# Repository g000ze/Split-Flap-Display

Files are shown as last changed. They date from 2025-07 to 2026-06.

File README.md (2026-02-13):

## Intro
Older people (like me) look back with nostalgia at train stations and airports, middle-aged people are captivated by technology, and the younger generation is excited by the clattering sound combined with the non-virtual movement. The split flap display remains a fascinating display panel for text and small animations.

One day, while watching a video about split flap displays, I suddenly felt the desire to own one. After a relatively short research, I realized that only a few manufacturers build such displays. There are, for example, [Oat Foundry](https://www.oatfoundry.com/), [Vestaboard](https://www.vestaboard.com/), [Scott Bezek](https://github.com/scottbez1/splitflap) or the one called "Split Flap Display Manufacturer." No matter which manufacturer you choose, the displays are either very expensive or don't meet my requirements. So I decided to try building one myself.

DIY Split Flap Display on YouTube (https://www.youtube.com/watch?v=Lept-73BvrE)

A typical split flap display looks best when it can display text. This text is naturally composed of characters, i.e., letters, numbers, and special characters. Optionally, symbols, colors, or images can also be displayed. A character is represented on the display by a so-called module. A module consists of a housing, a stepper motor, a motor driver, a PCB that connects the driver and the motor, a carousel, 50 flaps for the characters, and, of course, various spacers and screws that hold the whole thing together. A magnetic sensor (Hall effect sensor) is also integrated into the carousel, which tells the microprocessor when position 0 or the home position has been reached.

As already mentioned, a single module produces little effect, so we want multiple modules for a display to achieve an intense visual effect. I decided to control eight modules with an [Arduino Micro](https://docs.arduino.cc/hardware/micro/). The modules therefore always come in units of eight. The Micro offers 20 digital input/output pins. Two of these are required per module: an output pin as a stepper for the driver and an input pin for the Hall effect sensor to determine the feedback for a full rotation of the carousel. This means a total of 16 Arduino pins are used for eight modules. The Arduino, in turn, is placed on the backplane PCB, where the modules are plugged into so-called card edge connectors. This PCB primarily controls two things:
- The digital communication between the Arduino and the modules (drivers & Hall sensors)
- The power supply for all electronics, including the motors

**Animation of spinning spool using OpenSCAD**

Spinning Carousel (https://github.com/user-attachments/assets/af98eea6-6dcd-4d9f-962c-459cd9d655be)

[![Exploded View]](https://github.com/user-attachments/assets/ecffe0bf-9c8d-47f0-b8ce-c02ede4a916f)

## The Housing
The housing is used to position the motor, along with the carousel and flaps, as well as the PCB with the Hall sensor. If everything is exactly right, the flaps will drop at the right time and the magnet will move correctly over the sensor. I used 0.8 mm sheet steel for the housing. The 3D OpenSCAD drawing can be found [here](https://github.com/g000ze/Split-Flap-Display/blob/main/OpenSCAD/Chassis.scad). I found a company in Switzerland called [Blexon](https://blexon.com), that will punch and bend the housing according to my specifications.

Housing

## The Stepper Motor
Normally, Nema 17 stepper motors are mounted on the side where the shaft is located. This display is different; the motor must be mounted on one side, and the shaft, where the carousel is screwed to, must be on the opposite side. The [17HS13-0404D](https://www.omc-stepperonline.com/de/doppel-schacht-nema-17-bipolar-1-8deg-26ncm-36-8oz-in-0-4a-12v-42x34mm-4-draehte-17hs13-0404d) is the only Nema 17 I could find with the shaft on the opposite side from where it is mounted. This motor is actually a "dual shaft" motor. The 17HS13-0404D is powered by +12 volts.

17HS13-0404D

## The Driver
To operate a stepper motor, you need a driver. There are many. I experimented with stepper motor drivers for a long time until I finally came across the [TMC2208](https://www.digikey.ch/de/products/detail/watterott-electronic-gmbh/20170003-002/10071142) "Silent Step Stick" from [Watterott](https://learn.watterott.com/de/silentstepstick/). This driver allows the 17HS13-0404D to run almost silently. Finally, the sound of a split-flap display plays a crucial role. We want to hear only the flaps clattering, not the motors.

## The PCBs
Two different types of PCBs are required. One is a small PCB that is attached to each module. It essentially carries the driver and the Hall sensor. The other is the backplane PCB, which connects the Arduino's electronic wires to the eight modules via card-edge connectors. The six connections that run via the card-edge connectors are:
- Hall sensor
- GND
- +5V
- Step
- GND
- +12V

The TMC2208 and the Hall sensor on the module PCB each operate at +5 VCC, while the motor naturally requires 12 volts.

Module markiert
Backplane markiert

## The Carousel
The Carousel is attached to the pouley on the motor shaft so that it can be rotated by the steppermotor. It also holds the 50 flaps in position. The stepper motor is located inside the carousel. With its 82mm diameter, the carousel fits perfectly around the motor and there's enough space for the 50 flap positions. The two wheels are different, as the left wheel contains spokes, while the right wheel is open.

Carousel

I decided to use [3mm PVC plates](https://www.vink.ch/wa_files/Produktblatt_20PVC-U_20TROVIDUR_20EC_205_3_2015_20Ind.pdf) for the carousel. A company named [Waterjet](https://www.waterjet.ch/) located in Switzerland did the water cutting to cut out the carousel wheels.

## The Pouley
The pouley connects the motor and the carousel together. [This](https://www.pololu.com/product/1998) one was actually the only one I found to suit the motor shaft. So I bought it, even though it is insanely overpriced.

## The Flaps
The flaps are the essential parts, since they show the text that you want to see. Basically almost all kind of fonts, characters, signs and pictures are possible. After endless searching, trying and disapointments, I found a company named [Ren Peck](http://www.ren-peck.com/) in China who was willing to create what I am looking for. In fact it is the very same company that created the flaps for [Scott Bezek](https://github.com/scottbez1/splitflap)s Split Flap Display. 

Flaps

One flap has basically the size of 40mm height and 50mm width. There are two little notches on each side in order to hold them in the carousel and to make them actually flip down. 

Flaps Small

## The Software
The software was mainly written by me. See GitHub repository for details and ask me if you get any questions or suggestions regarding that.

## Other

## Tools Used
- OpenSCAD: https://openscad.org/
- KiCad: https://www.kicad.org/
- FreeCAD: https://www.freecad.org/
- For the Raspberry Pi to communicate with Arduino using I2C, I used this extension: https://github.com/tasoftch/php-i2c-extension

## Parts
### Module
Exploded_Split_Flap_Module

| Part | Nr. | Provider | Model | Link |
|---|-----|---|---|---|
| Housing | 1 | Blexon Galgenen | | https://blexon.com/ |
| Stepper Motor | 2 | Stepper Online | 17HS13-0404D | https://www.omc-stepperonline.com/de/doppel-schacht-nema-17-bipolar-1-8deg-26ncm-36-8oz-in-0-4a-12v-42x34mm-4-draehte-17hs13-0404d |
| Wheels for the Carousel | 3 | Waterjet Mörschwil  | | https://www.waterjet.ch/ |
| Flaps | 4 | Ren Peck China | | https://www.alibaba.com/product-detail/China-Ren-peck-supply-emotion-cards-60650877066.html |
| Pouley 5mm Shaft, M3 Holes | 5 | Eckstein | | https://eckstein-shop.de/PololuUniversalAluminumMountingHubfor5mmShaft2CM3Holes2-Pack or https://www.pololu.com/product/1998 |
| PCB | 6 | JLCPCB | | https://jlcpcb.com/ |
| Stepper Driver | 7 | Digikey | TMC2208 | https://www.digikey.ch/de/products/detail/analog-devices-inc-maxim-integrated/TMC2208SILENTSTEPSTICK/6873626 |
| Spacer Motor 20mm | 8 | Axxatronic | OG-PA-6-3,2-20  | https://www.axxatronic.de/distanzhuelsen/kunststoff/OG-PA-0060-0032.html |
| Spacer Carousel 51mm | 8 | Axxatronic | OG-PA-6-3,2-51  | https://www.axxatronic.de/distanzhuelsen/kunststoff/OG-PA-0060-0032.html |
| Spacer PCB 2mm | 8 | Axxatronic | OG-PA-6-3,2-02  | https://www.axxatronic.de/distanzhuelsen/kunststoff/OG-PA-0060-0032.html |
| Magnet | 9 | supermagnete.ch | S-02-02-N | https://www.supermagnete.ch/scheibenmagnete-neodym/scheibenmagnet-2mm-2mm_S-02-02-N |
| Screws | 10  | Schraubenking | | https://www.schraubenking.ch/ |

### Module PCB 
Module markiert

| Part | Nr. | Provider | Model | Link |
|---|-----|---|---|---|
| 10K Resistor | 1 | Digikey | CRGCQ1210F10K | https://www.digikey.ch/en/products/detail/te-connectivity-passive-product/CRGCQ1210F10K/8576485 |
| Header Connector | 2 | Digikey | NPPC082KFMS-RC  | https://www.digikey.ch/en/products/detail/sullins-connector-solutions/NPPC082KFMS-RC/776176 |
| Hall Sensor | 3 | Digikey | 620-1002-1-ND | https://www.digikey.ch/de/products/detail/allegro-microsystems/A1102LLHLT-T/1006577 |
| 47 µF Capacitor | 4 | Digikey | APA0606470M025R | https://www.digikey.ch/en/products/detail/kyocera-avx/APA0606470M025R/15195370 |
| Wires Connector | 5 | Digikey | 009176004873906 | https://www.digikey.ch/en/products/detail/kyocera-avx/009176004873906/8540378 |

### Backplane PCB 
Backplane markiert

| Part | Nr. | Provider | Model | Link |
|---|-----|---|---|---|
| Arduino Micro | 1 | Digikey | A000053 | https://www.digikey.ch/de/products/detail/arduino/A000053/4486332 |
| Voltage Converter | 2 | Digikey | R-78K5.0-1.0 | https://www.digikey.ch/en/products/detail/recom-power/R-78K5-0-1-0/18093047 |
| Card Edge Connector (old version) | 3 | Digikey | EDC305122-ND | https://www.digikey.ch/de/products/detail/edac-inc/305-012-520-202/107502 |
| Card Edge Connector (new version) | 3 | Digikey | EBC06DRXH | https://www.digikey.ch/de/products/detail/sullins-connector-solutions/EBC06DRXH/927248 |
| Connector Header for Arduino | 4 | Digikey | 1-215307-7 | https://www.digikey.ch/en/products/detail/te-connectivity-amp-connectors/1-215307-7/2278494 |
| Screw Terminal for 12V Power | 5 | Digikey | 282836-1 | https://www.digikey.ch/en/products/detail/te-connectivity-amp-connectors/282836-1/2222325 |

Generated by https://www.tablesgenerator.com/markdown_tables

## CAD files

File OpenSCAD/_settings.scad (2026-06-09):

/*

   Copyright Stefan Frech, 10.12.2021 - 28.09.2024
   Projekt Split-Flap Display Module

   Licensed under the Apache License, Version 2.0 (the "License");
   you may not use this file except in compliance with the License.
   You may obtain a copy of the License at

       http://www.apache.org/licenses/LICENSE-2.0

   Unless required by applicable law or agreed to in writing, software
   distributed under the License is distributed on an "AS IS" BASIS,
   WITHOUT WARRANTIES OR CONDITIONS OF ANY KIND, either express or implied.
   See the License for the specific language governing permissions and
   limitations under the License.
*/

$fn=100;

nr_of_flaps = 50;

// Flaps
flap_width = 50;
flap_height = 40;
flap_thickness = 0.76;
flap_pin = 3;
flap_total_width = flap_width + (2 * flap_pin);

// Karussell
carousel_diameter = 82;
carousel_thickness = 3;
carousel_inner_distance = 51;
carousel_flap_holes_diameter = 3.4;
carousel_flap_path_radius = 40 - (carousel_flap_holes_diameter/2);
carousel_axis_diameter = 5;
carousel_inner_circle = 24;
carousel_spokes_width = 10;
carousel_pos_x = 20.8;        // um 0.5mm nach vorne korrigiert am 08.08.2025, damit die Flaps etwas besser klemmen.
                              // um 0.2mm nach hinten korrigiert am 31.08.2025, weil das Gehäuse nun 1.0 und nicht mehr 0.8mm ist.
carousel_pos_y = -13.5;
carousel_pos = [carousel_pos_x,carousel_pos_y,0];

// Die Löcher werden etwas länger, damit die Darstellung von OpenSCAD stimmt
carousel_thickness_holes = carousel_thickness + 0.01;

// Ausschnitt
carousel_diameter_cutout = 59;

// Poulley
pulley_nr_of_holes = 4;
pulley_holes_diameter = 3;
pulley_holes_path_radius = 6.35;
pulley_diameter = 19;
pulley_thickness = 5;
pulley_axis_diameter = carousel_axis_diameter;

// Spacers Karussell
carousel_spacer_outer_diameter = 6;
carousel_spacer_inner_diameter = 3.2;
carousel_spacer_length = carousel_inner_distance;
carousel_spacer_nr = 4;
carousel_spacer_holes_diameter = 3.2;
carousel_spacer_path_radius = 33;

// Magnet
magnet_hole_diameter = 1.9;
magnet_hole_path_radius = carousel_spacer_path_radius;

// Die Schrauben durch die Karussell Spacer
carousel_spacer_screw_length = 60;
carousel_spacer_screw_diameter = 3;

// Stepper Motor
motor_width = 42;
motor_height = 42;
motor_depth = 34;
motor_corners = 5.5;
motor_axis_diameter = carousel_axis_diameter;
motor_axis_shift = -5;
motor_axis_length = 64;
motor_attachment_depth = 2;
motor_attachment_diameter = 22;
motor_winding_distance = 31;
// Spacer für Motor
motor_spacer_outer_diameter = 6;
motor_spacer_inner_diameter = 3.2;
motor_spacer_length = 20;
// Schrauben für die Befestigung des Motors
motor_screw_diameter = 3;
motor_screw_length = 25;

// Gehäuse
housing_width = 120;
housing_height = 150;
housing_outer_distance = 70;
//housing_thickness = 0.8;
housing_thickness = 1;
housing_inner_distance = housing_outer_distance - (2 * housing_thickness);

housing_cutout_height = 104;
housing_cutout_width = 53;
housing_cutout_small_height = 35;
housing_cutout_small_width = 3;
housing_cutout_position_y = 3;

// Das Loch für den Bolzen
housing_bolt_v = 26;
housing_bolt_h = 16;
housing_virt_bolt_pos = [37, 0, -71];


// PCB
pcb_width = 42.67;
pcb_length = 72;
pcb_edge_width = 17.2;
pcb_edge_length = 7.4;
pcb_thickness = 1.6;
pcb_copper_width = 1.7;

pcb_hole_diameter = 3.2;
// Die Position der Löcher im Gehäuse für das PCB sind jeweils
// gemessen an den hinteren Löchern für den Motor. 
// also: pcb_hole_top_from_left = 52 bedeutet, dass das obere Loch
// für das PCB 52mm vom hinteren Loch des Motors weg ist.
pcb_hole_top_from_left_housing = 52;
pcb_hole_bottom_from_left_housing = 27;

// Die Position der Löcher im PCB sind jeweils gemessen
// am linken Rand des PCB.
// pcb_hole_top_from_left_housing - pcb_hole_top_from_left_pcb = (motor_spacer_outer_diameter/2) + 0.5
// 52 - 48.5 = (6/2) + 0.5
pcb_hole_top_from_left_pcb = 48.5;
pcb_hole_bottom_from_left_pcb = 23.5;

// Hall Sensor
pcb_hall_top_from_left = 12.25;
pcb_hall_top_from_top  = 10.85;
pcb_hall_width  = 2.6;
pcb_hall_length = 3.1;
pcb_hall_height = 0.7;

// Das PCB soll mit Spacern etwas vom Gehäuse abstehen.
pcb_spacer_length = 2;
pcb_spacer_outer_diameter = 6;
pcb_spacer_inner_diameter = 3.2;

// Pin Header Sockets
pcb_pin_header_length=20.82;
pcb_pin_header_width=5.08;
pcb_pin_header_height=7.1;
pcb_pin_header_pin_distance=2.54;
pcb_pin_header_hole_diam=1;

pcb_pin_header_pos_x=7;
pcb_pin_header_pos_y1=28.8;
pcb_pin_header_pos_y2=13.5;


// always adjust overrides in _font_setup.scad accordingly
        
characters = [
     "0", "A", "B", "C", "D",
     "1", "E", "F", "G", "H",
     "2", "I", "J", "K", "L",
     "3", "M", "N", "O", "P",
     "4", "Q", "R", "S", "T",
     "5", "U", "V", "W", "X",
     "6", "Y", "Z", "+", "-",
     "7", "?", "!", ".", ",",
     "8", "@", ":", ";", "#",
     "9", "*", "$", "/", " ", 
];

/*
        characters = [
               "0", "1", "2", "3", "4", "5", "6", "7", "8", "9",
               "A", "B", "C", "D", "E", "F", "G", "H", "I", "J",
               "K", "L", "M", "N", "O", "P", "Q", "R", "S", "T",
               "U", "V", "W", "X", "Y", "Z", "!", "%", "&", "*",
               "+", "-", ".", "/", ":", "?", "$", "@", "#", " ",
        ];
*/


/*
  Settings for the flaps sheet
  These settings below take place at
  the following files:
  - Overallview.scad
  - Printview.scad
  - _font_setup.scad
  - 2D_library.scad
*/

include<_font_setup.scad>;

font_preset = "msgothicsfd";

letter_facet_number = 50;

// how many columns and rows to display
cols = 5;
//rows = 10;
rows = ceil(len(characters) / cols);

// horizontal space between flaps
h_space_between_flaps = 8;
// vertical space between flaps
v_space_between_flaps = 8;

outline_weight = 0.1;

// overlap letter for cutting tolerance
overlap = 4;

// Der Balken, der alles Überstehende abschneidet
cut_off_blind      = 4.5;

// the size of the foil
foil_width  = 360;
foil_height = 510;

// font size of description text
font_size_desc = 3;

// marker sizes
length_marker = 8;
width_marker  = 0.2;

indicator_position = 14;

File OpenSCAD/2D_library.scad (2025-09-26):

/*
   Copyright Stefan Frech, 10.12.2021 - 28.09.2024
   Projekt Split-Flap Display Module

   Licensed under the Apache License, Version 2.0 (the "License");
   you may not use this file except in compliance with the License.
   You may obtain a copy of the License at

       http://www.apache.org/licenses/LICENSE-2.0

   Unless required by applicable law or agreed to in writing, software
   distributed under the License is distributed on an "AS IS" BASIS,
   WITHOUT WARRANTIES OR CONDITIONS OF ANY KIND, either express or implied.
   See the License for the specific language governing permissions and
   limitations under the License.
*/

include<_settings.scad>;


module base_flap(overlap = 0)
{
    square([flap_width, flap_height + overlap], center = true);
}

module flap()
{
    base_flap();
    pins();
}

module flap_outline()
{
    difference()
    {
        offset(delta = +outline_weight) flap();
        flap();
    }
}

module pins()
{
    translate([ ((flap_width/2) + (flap_pin/2)), -((flap_height/2) - (flap_pin/2))])
    {
        square([flap_pin,flap_pin], center = true);
    }
    translate([-((flap_width/2) + (flap_pin/2)), -((flap_height/2) - (flap_pin/2))]) 
    {
        square([flap_pin,flap_pin], center = true);
    }
}

module pins_outline()
{
    difference()
    {
        offset(delta = +outline_weight) pins();
        pins();
        // lets make the inner line disapear with an additional square
        translate([0, -((flap_height/2) - (flap_pin/2))]) square([flap_width, flap_pin + (outline_weight * 2)], center = true);
    }
}

module foil()
{
    square([foil_width, foil_height], center = true);
}

module indicator_cross()
{
    square([width_marker, length_marker], center = true);
    square([length_marker, width_marker], center = true);
}

module indicators(){
    // Indicators for CAD initialisation
    h_pos = (foil_width  / 2) - indicator_position;
    v_pos = (foil_height / 2) - indicator_position;
    
    translate([ h_pos,  v_pos, 0]) indicator_cross();
    translate([-h_pos,  v_pos, 0]) indicator_cross();
    translate([-h_pos, -v_pos, 0]) indicator_cross();
    translate([ h_pos, -v_pos, 0]) indicator_cross();
}
    
module half_letter(col, row)
{
    difference()
    {
        intersection()
        {
            // this does the overlap of the letter
            //flap();
            base_flap(overlap);
            
            // mind front and back as well as last character
            if(side == "front")
            {
                rotate([0, 0]) translate([0, -(flap_height / 2)]) 
                    draw_letter(characters[(cols * row) + col]);
            }
            else
            {
                character = (cols * row) - col + cols == len(characters) ? 0 : (cols * row) - col + cols ;
                rotate([180, 180]) translate([0,  (flap_height / 2)]) 
                    draw_letter(characters[character]);
            }
        }
        // Das ist der Balken, der unten alles Überstehende abschneidet
        if(side != "front") translate([0, (flap_height/2) - (cut_off_blind/2)]) square([flap_width, cut_off_blind], center = true);
    }
}

module cols_and_rows()
{
    for(col=[0:1:cols-1])
    {
        for(row=[start_row-1:1:end_row-1])
        {
            // this translate shifts the objects in rows and cols
            translate([(flap_total_width + h_space_between_flaps) * col, -(flap_height + v_space_between_flaps) * (row - start_row)])
            {
                half_letter(col, row);
                flap_outline();
            }
        }
    }
}

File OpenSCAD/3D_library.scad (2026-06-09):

/*
   Copyright Stefan Frech, 10.12.2021 - 28.09.2024
   Projekt Split-Flap Display Module

   Licensed under the Apache License, Version 2.0 (the "License");
   you may not use this file except in compliance with the License.
   You may obtain a copy of the License at

       http://www.apache.org/licenses/LICENSE-2.0

   Unless required by applicable law or agreed to in writing, software
   distributed under the License is distributed on an "AS IS" BASIS,
   WITHOUT WARRANTIES OR CONDITIONS OF ANY KIND, either express or implied.
   See the License for the specific language governing permissions and
   limitations under the License.
*/

include<_settings.scad>;

module senk_schraube_m3(length) {
    // Schrauben Kopf Imbus (Sechskant)
    difference() 
    {
        cylinder(h=1.5, r1=3, r2=1.5, $fn=24*3);
        cylinder(h=0.8*3, r=1.15, $fn=6, center=true);
    }
    // Schraube ohne Gewinde, ist schneller.
    translate([0, 0, 1.5]) cylinder(d=3, h=length, center=false);
}

module mutter_m3(){
    difference(){
        cylinder(h=2.2, r=3, $fn=6, center=true);
        cylinder(h=2.2 + 0.1, r=1.5, center=true);
    }
}

module spacer(length, outer, inner)
{
    difference(){
        cylinder(d=outer, h=length,       center = true);
        cylinder(d=inner, h=length + 0.1, center = true);
    }
}

module karussell_scheibe_rechts(){
    difference(){
        cylinder(d=carousel_diameter, h=carousel_thickness, center = true);

        // Ring
        cylinder(d=carousel_diameter_cutout, h=carousel_thickness_holes, center = true);

        // Löcher für Flaps
        for(i=[1:nr_of_flaps]){
            translate([carousel_flap_path_radius*cos(i*(360/nr_of_flaps)),carousel_flap_path_radius*sin(i*(360/nr_of_flaps)),0]) cylinder(d=carousel_flap_holes_diameter, h=carousel_thickness_holes, center = true);
        }

        // Löcher Spacers
        for(i=[1:carousel_spacer_nr]){
            translate([carousel_spacer_path_radius*cos(i*(360/carousel_spacer_nr)),carousel_spacer_path_radius*sin(i*(360/carousel_spacer_nr)),0]) cylinder(d=carousel_spacer_holes_diameter, h=carousel_thickness_holes, center = true);
        }

        // 2mm Loch für das Magnet und als Alignement
        x=(360 / nr_of_flaps * 7);
        translate([magnet_hole_path_radius*cos(x),magnet_hole_path_radius*sin(x),0]){
            cylinder(d=magnet_hole_diameter, h=carousel_thickness_holes, center = true);
        }
    }
}

module karussell_scheibe_links()
{
    difference()
    {
        union()
        {
            karussell_scheibe_rechts();
            // Die beiden Speichen
            cube([carousel_spokes_width, carousel_diameter_cutout, carousel_thickness], center = true);
            cube([carousel_diameter_cutout, carousel_spokes_width, carousel_thickness], center = true);
            // Der Kreis wo die Löcher für das Poulley und die Achse rein kommen
            cylinder(d=carousel_inner_circle, h=carousel_thickness, center = true);
        }

        // Loch für Achse
        cylinder(d=carousel_axis_diameter, h=carousel_thickness_holes, center = true);

        for(i=[1:pulley_nr_of_holes])
        {
            // Löcher für Motor Poulley
            translate([
                pulley_holes_path_radius * cos(i * (360 / pulley_nr_of_holes)),
                pulley_holes_path_radius * sin(i * (360 / pulley_nr_of_holes)),
                0
            ]) cylinder(d=pulley_holes_diameter, h=carousel_thickness_holes, center = true);
        }
    }
}

module karussell_scheibe_position(side = "rechts")
{
    // z-Offset
    zoffset = (carousel_inner_distance/2 + carousel_thickness/2) * (side == "rechts" ? -1 : 1);
    
    rotate([90,90,0])
    translate([0,0,zoffset]) {
        if (side == "rechts") karussell_scheibe_rechts();
        else                  karussell_scheibe_links();
    }
}

module karussell_schrauben(){
    rotate([90, 0, 0]){
        for(i=[1:carousel_spacer_nr]){
            translate([carousel_spacer_path_radius*cos(i*(360/carousel_spacer_nr)), carousel_spacer_path_radius*sin(i*(360/carousel_spacer_nr)), -((carousel_inner_distance/2)+carousel_thickness+0.2)]){
                senk_schraube_m3(carousel_spacer_screw_length);
            }
        }
    }
}

module karussell_muttern(){
    rotate([90, 0, 0]){
        for(i=[1:carousel_spacer_nr]){
            translate([carousel_spacer_path_radius*cos(i*(360/carousel_spacer_nr)), carousel_spacer_path_radius*sin(i*(360/carousel_spacer_nr)), ((carousel_inner_distance/2)+carousel_thickness+1.1)]){
                mutter_m3();
            }
        }
    }
}

module karussell_spacer(){
    rotate([90,0,0]){
        for(i=[1:carousel_spacer_nr]){
            translate([carousel_spacer_path_radius*cos(i*(360/carousel_spacer_nr)),carousel_spacer_path_radius*sin(i*(360/carousel_spacer_nr)),0]){
                spacer(carousel_spacer_length, carousel_spacer_outer_diameter, carousel_spacer_inner_diameter);
            }
        }
    }
}

module odd_flap_bottom(){
    rotate([0,0,51*1.2]){
        translate([(carousel_flap_path_radius+(flap_height/2)-1.5),0,0]){
            rotate([90,0,0]){
                flap();
            }
        }
    }
}

module example_flap_front_top(){
    translate([carousel_flap_path_radius, -((flap_height/2)-1.5), 0]){
        rotate([90,0,270]){
            flap();
        }
    }
}

module example_flap_front_bottom(){
    translate([(carousel_flap_path_radius - (flap_thickness/2)),((flap_height/2) + carousel_flap_holes_diameter),0]){
        rotate([90,0,90]){
            flap();
        }
    }
}

module example_flap_bottom(number){
    translate([0, (flap_height/2) + (carousel_flap_path_radius - (carousel_flap_holes_diameter / 2)) , 0]){
        rotate([90,0,90]){
            flap_with_char(number);
        }
    }
}

module stepper_motor(){
    translate([0,0,-((housing_inner_distance/2)-(motor_depth/2)-motor_spacer_length)]){
        difference(){
            cube([motor_width,motor_height,motor_depth], center = true);
            // Ecken
            translate([motor_width/2,motor_height/2,0])    rotate([0,0,45]) cube([motor_corners,motor_corners,motor_depth+0.1], center = true);
            translate([-motor_width/2,motor_height/2,0])   rotate([0,0,45]) cube([motor_corners,motor_corners,motor_depth+0.1], center = true);
            translate([motor_width/2,-motor_height/2,0])   rotate([0,0,45]) cube([motor_corners,motor_corners,motor_depth+0.1], center = true);
            translate([-motor_width/2,-motor_height/2,0])  rotate([0,0,45]) cube([motor_corners,motor_corners,motor_depth+0.1], center = true);
            
            // Die Befestigungsgewinde
            translate([ motor_winding_distance/2,  motor_winding_distance/2, 0]) rotate([0,0,45]) cylinder(d=motor_screw_diameter, h=motor_depth + 0.1, center = true);
            translate([-motor_winding_distance/2,  motor_winding_distance/2, 0]) rotate([0,0,45]) cylinder(d=motor_screw_diameter, h=motor_depth + 0.1, center = true);
            translate([ motor_winding_distance/2, -motor_winding_distance/2, 0]) rotate([0,0,45]) cylinder(d=motor_screw_diameter, h=motor_depth + 0.1, center = true);
            translate([-motor_winding_distance/2, -motor_winding_distance/2, 0]) rotate([0,0,45]) cylinder(d=motor_screw_diameter, h=motor_depth + 0.1, center = true);
        }

        // Aufsatz
        translate([0,0,-((motor_depth/2)+(motor_attachment_depth/2))]) cylinder(d=motor_attachment_diameter, h=motor_attachment_depth, center = true);
        
        //Achse
        translate([0,0,motor_axis_shift]) cylinder(d=motor_axis_diameter, h=motor_axis_length, center = true);
    }
}

module stepper_spacer(){
    spacer_pos = ((housing_inner_distance/2)-(motor_spacer_length/2));
    translate([motor_winding_distance/2,motor_winding_distance/2,-spacer_pos]){
        spacer(motor_spacer_length, motor_spacer_outer_diameter, motor_spacer_inner_diameter);
    }
    translate([-motor_winding_distance/2,motor_winding_distance/2,-spacer_pos]){
        spacer(motor_spacer_length, motor_spacer_outer_diameter, motor_spacer_inner_diameter);
    }
    translate([motor_winding_distance/2,-motor_winding_distance/2,-spacer_pos]){
        spacer(motor_spacer_length, motor_spacer_outer_diameter, motor_spacer_inner_diameter);
    }
    translate([-motor_winding_distance/2,-motor_winding_distance/2,-spacer_pos]){
        spacer(motor_spacer_length, motor_spacer_outer_diameter, motor_spacer_inner_diameter);
    }
}
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

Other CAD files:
OpenSCAD/_font_setup.scad
OpenSCAD/Carousel_left.scad
OpenSCAD/Carousel_right.scad
OpenSCAD/Chassis.scad
OpenSCAD/Overallview.scad
OpenSCAD/PVC_Plate.scad
OpenSCAD/Printview.scad
OpenSCAD/Split_Flap_Module.scad

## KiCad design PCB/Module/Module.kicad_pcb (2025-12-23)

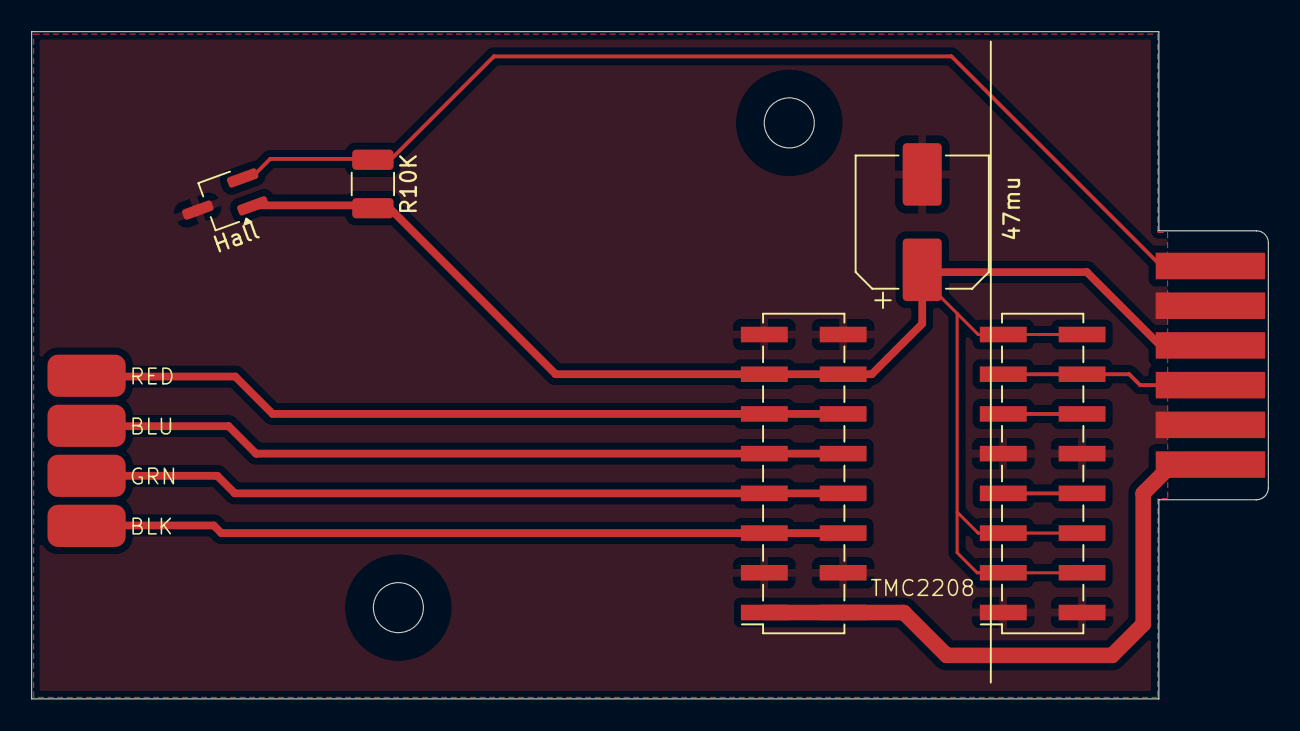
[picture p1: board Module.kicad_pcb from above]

Board: 2 copper layers, 79.1 x 42.7 mm, 5 parts (0 on the bottom side), 11 nets.

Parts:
47mu: CP_Elec_8x5.4
 : PinSocket_2x08_P2.54mm_Vertical_SMD
 #2: PinSocket_2x08_P2.54mm_Vertical_SMD
Hall: SOT-23W_Handsoldering
R10K: R_1210_3225Metric_Pad1.30x2.65mm_HandSolder

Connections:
+5V: 47mu.1, .13, .14, #2.3 MS1, #2.4 MS1, #2.5 MS2, #2.6 MS2, #2.15 Dir, #2.16 Dir, Hall.1, R10K.2
+12V: .1, .2
A1: .9, .10
A2: .11, .12
B1: .7, .8
B2: .5, .6
Clock: #2.11, #2.12
GND: 47mu.2, .3, .4, .15, .16, #2.1 Enable, #2.2 Enable, #2.9 PDN, #2.10 PDN, Hall.3
Hall: Hall.2, R10K.1
NC: #2.7, #2.8
Step: #2.13, #2.14

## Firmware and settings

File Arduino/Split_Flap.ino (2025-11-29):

#include <Wire.h>

// motor and flap settings
const byte microsteps = 16;   // Microsteps for the driver
const byte motorsteps = 200;  // Stepper motor takes 200 positions per revolution
const byte flaps = 50;        // number of flaps on carrousel
const int ms_per_revolution = motorsteps * microsteps; // microsteps performed by carousel revolution
const int ms_per_flap = ms_per_revolution / flaps; // microsteps performed by flap position

/*
 Speed: The greater the number the slower it turns.
 28800 / microsteps is approximately 6 seconds per revolution.

 grundsätzlich ist jede Geschwindigkeit möglich, solange
 sie sich durch 32 (Anz. max. Microsteps) teilen lässt.
 sneak:  128000
 slow:   38400
 normal: 28800
 fast:   19200
 stress: 9600
 */
const unsigned long speed = 28800 / microsteps;

// Number of modules
const byte modules = 8;

// Arduino pin settings
// as of Backplane V3 PCB
#include <inputs/pins_v2.ino>
// input settings
#include <inputs/inputs_v2.ino>

const byte hall_pin[modules] =
{
    hall_pin_0,
    hall_pin_1,
    hall_pin_2,
    hall_pin_3,
    hall_pin_4,
    hall_pin_5,
    hall_pin_6,
    hall_pin_7,
};

const byte step_pin[modules] =
{
    step_pin_0,
    step_pin_1,
    step_pin_2,
    step_pin_3,
    step_pin_4,
    step_pin_5,
    step_pin_6,
    step_pin_7,
};

// some other things
unsigned long curr_time = 0;
unsigned long prev_time = 0;

int  cur_ms_pos[modules]          = {};
int  new_ms_pos[modules]          = {};
int  ms_to_go[modules]            = {};
char new_char[modules]            = {};
bool set_ms_pos[modules]          = {};

// Feineinstellung
const int UNSET = -1;
int init_ms_pos[modules] = {UNSET, UNSET, UNSET, UNSET, UNSET, UNSET, UNSET, UNSET};
//const int init_ms_pos[modules]   = {20, 20, 20, 20, 20, 20, 20, 20};

// read values out of EEPROM
#include <EEPROM.h>
const int i2c_addr            = EEPROM.read(0);
const int default_init_ms_pos = EEPROM.read(1);

void setup() {
  Serial.begin(9600);

  // Join I2C bus as slave with uniqe address
  Wire.begin(i2c_addr);
  // set I2C receive and request functions
  Wire.onReceive(receive_i2c_event);
  Wire.onRequest(request_i2c_event);

  // setup pins and variables
  for(byte module = 0; module < modules; module++){
    pinMode(step_pin[module], OUTPUT);
    pinMode(hall_pin[module], INPUT);

    // ascii 32 is space character
    new_char[module] = 32;
    cur_ms_pos[module] = 0;
    set_ms_pos[module] = false;
    set_ms_to_go(module);

    if (init_ms_pos[module] == UNSET) {
      init_ms_pos[module] = default_init_ms_pos;
    }
  }
}

// ToDo XXX
#include <output/output.ino>

void loop() {
  motor_run();
  receive_serial_event();
}

void motor_run(){
  curr_time = micros();
  if((curr_time - prev_time) >= speed){
    prev_time = curr_time;
    for(byte module = 0; module < modules; module++){
      if(ms_to_go[module] > 0){
        digitalWrite(step_pin[module], HIGH);
        digitalWrite(step_pin[module], LOW);
        update_ms_pos(module);
      }
    }
  }
}

void update_ms_pos(byte module){
  cur_ms_pos[module]++;
  ms_to_go[module]--;

  // reset cur_ms_pos only once if magnet is at home place
  if(is_magnet_home(module)){
    if(set_ms_pos[module]){
      // uncomment for debugging purposes.
      /*      
      if(cur_ms_pos[module] > ms_per_revolution){
        Serial.print("magnet behind counter ");
      }
      if(cur_ms_pos[module] < ms_per_revolution - 1){   // weshalb - 1 ?
        Serial.print("magnet before counter ");
      }
      */

      cur_ms_pos[module] = 0;

      // instant adjustment of microsteps to go
      if(new_ms_pos[module] != ms_per_revolution){
        set_ms_to_go(module);
      }else{
        ms_to_go[module] = init_ms_pos[module];
      }
    }
    set_ms_pos[module] = false;
  }else{
    /*
    // wait for magnet after one revolution
    if(cur_ms_pos[module] >= ms_per_revolution){
      if(cur_ms_pos[module] <= (ms_per_revolution * 3)){
        ms_to_go[module] = 1;
      }
    }
    */
    set_ms_pos[module] = true;
  }
}

/*
case 1:
if new position is greater than current position, go straight forward
positions to walk = new - cur
cur = 6
new = 30
30 - 6 = 24

case 2:
if new position is smaller than current position, recalculate respecting flap positions
positions to walk = (flaps - cur) + new
cur = 44
new = 30
(50 - 44) + 30 = 36
*/
void set_ms_to_go(byte module){
  unsigned int new_flap_pos = get_position(new_char[module]);
  // proceed only if a valid character has been provided
  if(new_flap_pos == 0){
    return;
  }

  new_ms_pos[module] = new_flap_pos * ms_per_flap;

  // pretend to be on correct position, even if magnet has not been spotted
  int position = cur_ms_pos[module] % ms_per_revolution;

  // do the magic!
  if(new_ms_pos[module] > position){
    ms_to_go[module] = new_ms_pos[module] + init_ms_pos[module] - position;
  }else{
    ms_to_go[module] = new_ms_pos[module] + init_ms_pos[module] + (ms_per_revolution - position);
  }
}

bool is_magnet_home(byte module) {
  return (digitalRead(hall_pin[module]) == 0);
}

bool is_running(byte module) {
  return (ms_to_go[module] > 0);
}

/*
 * serial events
 */

void receive_serial_event() {
  if (!Serial.available()) {
    return;
  }

  String content = Serial.readStringUntil('\n');
  for (byte module = 0; module < modules && module < content.length(); module++) {
    new_char[module] = content.charAt(module);
    set_ms_to_go(module);
  }
}

/*
 * I2C events
 */
void receive_i2c_event(int bytes) {
  // register byte verwerfen
  Wire.read();

  // Maximal nur `modules` Bytes einlesen
  for (byte module = 0; module < modules && Wire.available(); module++) {
    byte b = Wire.read();

    // nur druckbare ASCII-Zeichen akzeptieren
    // https://www.eso.org/~ndelmott/ascii.html
    if (b >= 0x20 && b <= 0x7E) {
      new_char[module] = b;
      set_ms_to_go(module);
    }
  }

  // Rest verwerfen falls mehr als 8 Bytes geschickt wurden
  while (Wire.available()) Wire.read();
}

void request_i2c_event(){
  for(byte module = 0; module < modules; module++){
    if(ms_to_go[module] > 0){
      Wire.write(255);
    }else{
      //round, in case something ran out of count
      Wire.write(round((float)(cur_ms_pos[module] - init_ms_pos[module]) / ms_per_flap));
      //Wire.write((cur_ms_pos[module] - init_ms_pos[module]) / ms_per_flap);
    }
  }
}

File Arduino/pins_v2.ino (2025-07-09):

const byte hall_pin_0 = 18;
const byte hall_pin_1 = 19;
const byte hall_pin_2 = 20;
const byte hall_pin_3 = 21;
const byte hall_pin_4 = 9;
const byte hall_pin_5 = 10;
const byte hall_pin_6 = 11;
const byte hall_pin_7 = 12;

const byte step_pin_0 = 15;
const byte step_pin_1 = 14;
const byte step_pin_2 = 23;
const byte step_pin_3 = 22;
const byte step_pin_4 = 5;
const byte step_pin_5 = 4;
const byte step_pin_6 = 17;
const byte step_pin_7 = 16;

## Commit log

2023-01-22 add PHP code and library, that communicates with arduino.
2023-01-22 Add arduino code and create separate directories.
2024-09-28 added OpenSCAD files with animated module
    [Split_Flap_Module.scad, library.scad]
2024-10-08 make spinning carousel faster
    [Split Flap Module.scad, library.scad]
2024-10-11 small changes in code
    [Split_Flap_Module.scad, library.scad]
2024-11-06 new version with spinning carousel and optimized code
    [2D_library.scad, 3D_library.scad, Carousel_left.scad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]
2024-11-06 add license text
    [2D_library.scad, Carousel_left.scad, Carousel_right.scad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]
2024-11-07 add _font_setup.scad and _settings.scad
    [_font_setup.scad, _settings.scad]
2024-11-07 correct counter in 3D rotating_carousel module and move settings.scad to _settings.scad
    [2D_library.scad, 3D_library.scad, Carousel_left.scad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]
2024-11-15 Update README.md with better animated GIF
    better animated GIF with spinning carousel and printed flaps
2024-11-15 added start_row and end_row support. Little code cleanup.
    [2D_library.scad, 3D_library.scad]
2024-11-15 add render() to PVC picture for better preview performance
    [PVC_Plate.scad]
2024-11-15 Replace MS-Gothic with better font
    [_font_setup.scad, _settings.scad]
2024-11-22 Cut off blind only for backside flaps
    [2D_library.scad]
2024-11-22 modify module flap_with_char and add module draw_half_letter
    [3D_library.scad]
2024-11-22 count by rows and cols instead of cols and rows. Small difference, big impact.
    [Overallview.scad]
2024-11-22 add support for printing squares and colors
    [_font_setup.scad]
2024-11-24 fix wrong translate in rotating_carousel module of 3D library
    [3D_library.scad]
2024-11-29 remove MS Gothic font from _font_setup.scad
    [_font_setup.scad]
2024-12-01 small code style adjustments
    [_font_setup.scad]
2024-12-01 Code optimization and beautifying
    [3D_library.scad]
2024-12-02 small corrections for settings, remove obsolete font
    [_font_setup.scad, _settings.scad]
2024-12-05 add example_flaps_bolt to Split_Flap_Module.scad
    [Split_Flap_Module.scad]
2024-12-05 new settings for PCB
    [_settings.scad]
2024-12-05 new code for PCB and adjust code for motor position
    [3D_library.scad]
2024-12-06 add KiCad PCB files
    [Backplane.kicad_pcb, Module.kicad_pcb]
2025-01-01 fix error in Split_Flap.ino and simplify code in inputs.ino
    [Split_Flap.ino, inputs.ino]
2025-04-13 small code changes
    [3D_library.scad, PVC_Plate.scad, Split_Flap_Module.scad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]
2025-05-04 add exploded view of Split Flap Module
    [3D_library.scad, Printview.scad, Split_Flap_Module.scad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]
2025-05-10 get rid of confusing side effects when drawing flaps with half letters
    [3D_library.scad]
2025-05-22 new PHP library, supporting multiple arduinos
2025-06-28 add spacers between housing and pcb
    [3D_library.scad, _settings.scad]
2025-06-28 add the 'wipe to the end' function
    [Split_Flap_Module.scad]
2025-07-08 update module PCB with 3D wires connector
    [SplitFlap.kicad_pcb]
2025-07-08 rename module PCB files from SplitFlap.kicad to Module.kicad
    [Module.kicad_pcb]
2025-07-08 update backplane PCB
    [Backplane.kicad_pcb]
2025-07-23 set PDN pin on stepper driver to GND
    [SplitFlap.kicad_pcb]
2025-08-16 update backplane PCB with I2C connectors and new 3D models
    [Backplane.kicad_pcb]
2025-08-23 add virtual bolt to show better flaps behaviour in OpenSCAD animation
    [3D_library.scad, Carousel_left.scad, Carousel_right.scad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]
2025-08-23 code cleanup. move colors from library to Split_Flap_Module.scad. Remove unneeded modules and snippets.
    [3D_library.scad, Printview.scad, Split_Flap_Module.scad]
2025-08-23 separate module chassis_bolt to chassis_bolt_screw and chassis_bolt_nut
    [3D_library.scad]
2025-08-24 remove unneeded fn variables. Simplify code. Add faster version of karussell_scheibe with linear_extrude.
    [3D_library.scad]
2025-08-25 add simpler module for carousel library
    [3D_library.scad]
2025-08-25 add description
    [Carousel_left.scad, Printview.scad]
2025-08-25 add new settings for new carousel module. Also add more description. Reduce letter_facet_number for faster rendering.
    [_settings.scad]
2025-08-31 fix small failure where the hole for the axis gets executet four times instead of one time
    [3D_library.scad]
2025-09-26 rename array from chars to characters
    [2D_library.scad]
2025-09-26 remove old code, rename array from chars to characters, simplify code with ternary operators
    [3D_library.scad]
2025-09-26 remove empty line
    [PVC_Plate.scad]
2025-09-26 replace white flap with '/' character instead of 'w'.
    [_font_setup.scad]
2025-10-05 remove translate if explode > 0
    [Split_Flap_Module.scad]
2025-10-05 remove 'check' module. Correct 'flap_with_char' module, so that the last flaps display correctly. Give 'example_flap_bottom' module the possibility to display any flap.
    [3D_library.scad]
2025-10-05 add fully colored flaps example
    [_font_setup.scad]
2025-11-29 remove unneeded delay in motor_run function
2025-12-23 update PCB to newest version, remove obsolete files
    [Module.kicad_pcb, SplitFlap.kicad_pcb]
2026-01-18 Replace PCB images in README
    Updated images for Module PCB and Backplane PCB sections.
2026-01-18 Remove PCB images from README
    Removed two images related to the PCB module and backplane from the README.
2026-06-09 add pin headers on PCB. fix white shadow on flap spool.
    [3D_library.scad, Chassis.scad, _font_setup.scad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]
